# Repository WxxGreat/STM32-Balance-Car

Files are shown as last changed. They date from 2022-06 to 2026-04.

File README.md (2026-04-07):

# 0. 关于本项目

本项目使用`STM32F103C8T6`作为主控，`Keil5`开发，`Mahony`算法进行姿态解算的平衡车。项目中给出了`MPU6050`、`ICM20602`、`ICM42605`三种主流IMU的驱动。目前仅实现了直立平衡，建议当成工程模板使用。
 (＠_＠;)

# 1. 硬件

## 1.1 PCB 

目前是第一版，用到的都是插接件。后续还会更新PCB（计划换成贴片，体积会更小）

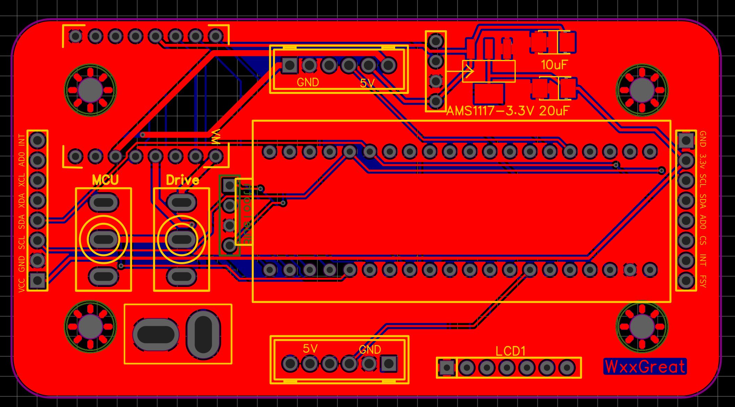
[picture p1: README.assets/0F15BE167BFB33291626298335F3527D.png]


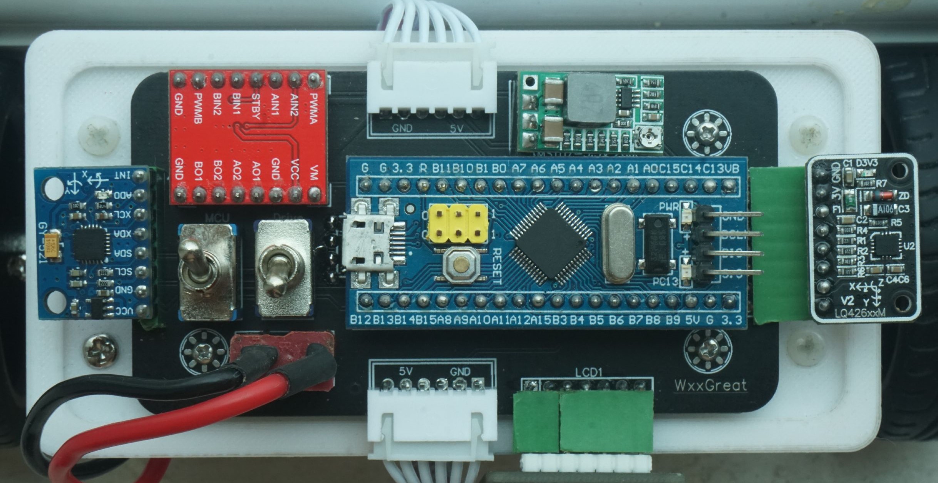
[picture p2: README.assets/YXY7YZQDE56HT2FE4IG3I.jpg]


## 1.2 车模

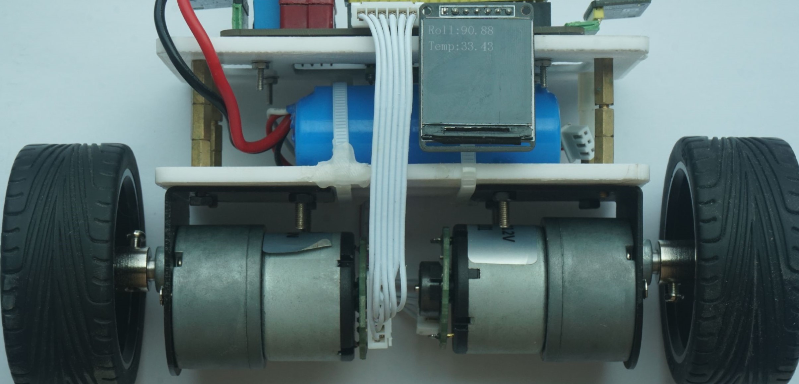
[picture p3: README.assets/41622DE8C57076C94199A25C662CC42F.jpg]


`LCD`使用1.3寸`ST7789`主控 `240×240`分辨率

电机型号`MG513P20_12V` ，我买的淘宝店：[直流减速电机带光电霍尔编码器码盘测速两轮自平衡小车 ](https://item.taobao.com/item.htm?spm=a1z10.3-c-s.w4002-15726392041.27.16a3143eqzsQfR&id=45347924687 )*

电池链接：[恩智浦智能汽车竞赛 正品BCDEFHLM车模2S锂电池及充电器](https://item.taobao.com/item.htm?spm=a1z10.3-c-s.w4002-22508770840.25.3b1949cceHXuh9&id=610152052172 )*

SolidWorks画的简单底板尺寸如图，用3D打印机制造

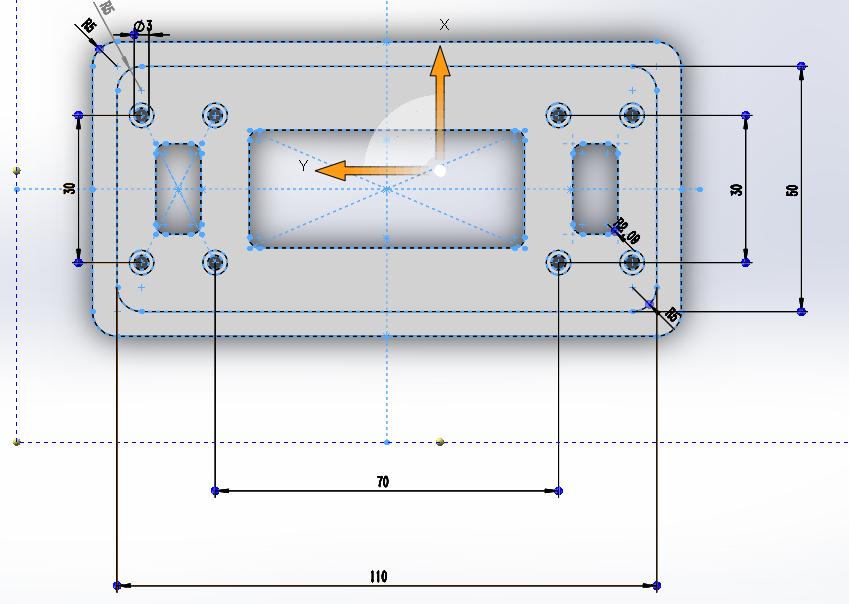
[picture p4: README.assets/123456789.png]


# 2. 算法

## 2.1 `PID`算法

####   2.1.1理论分析

该项目为使的小车平衡最主要的两个环就是直立环和速度环，通过叠加得到最终给电机的输出，这也是网上绝大多数的小车平衡控制方法。

1. 我们先使用常规的速度负反馈算法想象一下。首先我们给定一个目标速度值，由于小车在直立控制的作用下，此时小车要向前倾斜以获取加速度，车轮需要往后运动，这样小车速度就会下降。因为是负反馈,速度下降之后，速度控制的偏差增大，小车往前倾斜的角度增大，如此反复，小车便会倒下。
2. 为保证直立控制的优先级，我们把速度控制放在直立控制的前面，也就是速度控制调节的结果仅仅是改变直立控制的目标值。因为根据经验可知，小车的运行速度和小车的倾角是相关的。比如要提高小车向前行驶的速度，就需要增加小车向前倾斜的角度，倾斜角度加大之后，车轮在直立控制的作用下需要向前运动。因此直立环的`Kp`后面乘的值并不是`当前角度-机械中值`，而是一个我们速度的期望。**（这个理解了很重要！！！！）**

$$
a_1=Kp*(\theta-a_2)+Kd*\theta'  \qquad···································①直立环
$$

$$
a_2=Kp_1* Err_{speed}+Ki_1 * \sum Err_{speed}\space   \qquad····························②速度环
$$

**合并一下就可以得到：**

$$
a=Kp*(\theta)+Kd*\theta'-Kp \left [kp_1 * Err_{speed}+ki_1 * \sum Err_{speed} \right ] \qquad········③最终式
$$

因此在代码实现上我们就可以实现两个环的直接相加或相减，在`TIM3`定时器中`10ms`一个周期进行控制。

```c
      Balance_PID_Result = Position_PID_Cal(&Balance_PID, imu.Roll + 0.3f);
      if (Time_GAP_20ms) Velocity_PID_Result = Position_PID_Cal(&Velocity_PID, Velocity);

      PID_Result = Balance_PID_Result + Velocity_PID_Result;
      Set_Motor_Speed(PID_Result, PID_Result);
```

####   2.1.2调参经验

根据上边的分析我们只需要分别调整直立环的`Kp，kd`和速度环的`Kp，Ki`

1. 对于直立环的`Kp`，是调整最方便观察现象的，太小时小车没有足够的恢复力，太大时小车会在中值附近大幅震荡，调整到一个略微震荡的值即可
2. 直立环的`Kd`作用是减小低频振荡，但`Kd`太大小车又会造成高频振动，从小到大增大`Kd`，直到小车出现小幅高频振荡
3. 直立环调整结束后小车可以平衡，但受到扰动便会往一个方向疯跑，现在引入直立环
4. 网上查到的资料对于速度环`Ki = Kp/200` ，但在我的实际调整中最终确定了`Ki = Kp/100`，这个看自己小车了，可以先按照`Ki = Kp/200`去调
5. 先将直立环`Kp，Kd`同时×0.8。调整速度环`Kp`，速度环`Kp`越大，小车便越不会出现向一个方向狂奔的情况（因为速度被速度环控住了），但会减弱直立环的控制效果，因此调整到一个车受到干扰会摇摇晃晃停下的一个状态。
6. 摇摇晃晃的原因就是因为速度环`Kp`太大，回调速度环`Kp`，并且增大直立环`Kd`（想想`Kd`的作用是什么呢？）

**以上就是我调参的经验，可以参考，最好可以理解原理再去上手实践。**

## 2.2 `Mahony`算法

**参考一篇文章：[基于Manony滤波算法的姿态解算](https://blog.csdn.net/weixin_44821644/article/details/108542178)**

###   2.2.1IMU（以MPU6050举例）

`MPU6050`是一个集成了陀螺仪和加速度计的传感器，它能输出在直角坐标系下的`x，y，z`轴的角速度和加速度数据。

陀螺仪输出的格式为：绕`x`轴的旋转角速度，绕`y`轴的角速度，绕`z`轴的角速度（分别称为`roll`角速度，pitch角速度和`yaw`角速度）。

加速度计输出的格式为：`x`轴的加速度，`y`轴的加速度，`z`轴的加速度。

另外还需要关注传感器的其他参数如：

- 陀螺仪的量程：`eg.±2000dps`
- 加速度计的量程：`eg.±2g`
- `ADC`转换精度为`16bit`
- 传感器采样率`4-1000hz：eg.1000hz`

我们从IMU那就得到了陀螺仪数据`gx,gy,gz`，加速度数据`az,ay,az`

螺仪转换精度**2^16=65536   ,  65536/{2000-(-2000)}=16.4,实际1°等于ADC值16.4**

采样率就是数据的更新率，也就是我们每次读取数据的频率。

首先将陀螺仪的数据转换成角度，这里封装成一个函数

###   2.2.2算法实现

```c
static void Get_IMU_Values(float *values)
{
	int16_t gyro[3],acc[3];
	IMU_readGyro_Acc(&gyro[0],&acc[0]);
	for(int i=0;i<3;i++)
	{
        //gyro range +-2000; adc accuracy 2^16=65536; 65536/4000=16.4;
		values[i]=((float) gyro[i])/16.4f;	
		values[3+i]=(float) acc[i];
	}
}
```

**然后编写函数实现计算姿态角的功能，使用四元数计算姿态角的公式在理论分析中推导：**

**其中α为绕x轴旋转角即`roll`，β为绕y轴旋转角即`pitch`，γ为绕z轴旋转角即yaw。`a,b,c,d`即`q0,q1,q2,q3`.**

```c
void IMU_Update(void)
{
	static float q[4];
	float Values[6];	
	Get_IMU_Values(Values);	
	
	//change angle to radian,the calculate the imu with Mahony
	MahonyAHRSupdateIMU(Values[0] * PI/180, Values[1] * PI/180, Values[2] * PI/180,
 	                    Values[3], Values[4], Values[5]);		
	//save Quaternion
	q[0] = q0;
	q[1] = q1;
	q[2] = q2;
	q[3] = q3;
    
	imu.ax = Values[3];
	imu.ay = Values[4];
	imu.az = Values[5];
    
	imu.Pitch_v = Values[0];
	imu.Roll_v = Values[1];
	imu.Yaw_v = Values[2];

	//calculate the imu angle with quaternion
	imu.Roll = (atan2(2.0f*(q[0]*q[1] + q[2]*q[3]),1 - 2.0f*(q[1]*q[1] + q[2]*q[2])))* 180/PI;	
	imu.Pitch = -safe_asin(2.0f*(q[0]*q[2] - q[1]*q[3]))* 180/PI;
	imu.Yaw = -atan2(2 * q1 * q2 + 2 * q0 * q3, -2 * q2*q2 - 2 * q3 * q3 + 1)* 180/PI;
}
```

**代码中`MahonyAHRSupdateIMU()`函数实现的就是四元数的更新算法。**

*逻辑上，首先用加速度计校准陀螺仪，方式是通过计算当前四元数姿态下的重力分量，与加速度计的重力分量作叉积，得到误差。
对误差作P(比例)和I(积分)运算后加到陀螺仪角速度上。最终由角速度计算新的四元数。*

**代码中的 `sampleFreq` 即执行姿态解算的频率，这里用定时器，以500HZ的频率调用`get_angle();`**

```c
void MahonyAHRSupdateIMU(float gx, float gy, float gz, float ax, float ay, float az) {
	float recipNorm;	
	float halfvx, halfvy, halfvz;	//1/2 重力分量
	float halfex, halfey, halfez;	//1/2 重力误差
	float qa, qb, qc;
	//对加速度数据归一化
	recipNorm = invSqrt(ax * ax + ay * ay + az * az);
	ax *= recipNorm;
	ay *= recipNorm;
	az *= recipNorm;

	// 由四元数计算重力分量
	halfvx = q1 * q3 - q0 * q2;
	halfvy = q0 * q1 + q2 * q3;
	halfvz = q0 * q0 - 0.5f + q3 * q3;

	// 将四元数重力分量 与 加速度计重力分量 作叉积 得到误差
	halfex = (ay * halfvz - az * halfvy);
	halfey = (az * halfvx - ax * halfvz);
	halfez = (ax * halfvy - ay * halfvx);

	//对误差作积分
	integralFBx += twoKi * halfex * (1.0f / sampleFreq);	
	integralFBy += twoKi * halfey * (1.0f / sampleFreq);
	integralFBz += twoKi * halfez * (1.0f / sampleFreq);
	//反馈到角速度
	gx += integralFBx;	     gy += integralFBy;       gz += integralFBz;

	// 对误差作比例运算并反馈
	gx += twoKp * halfex;    gy += twoKp * halfey;    gz += twoKp * halfez;

	// 计算1/2 dt
	gx *= (0.5f * (1.0f / sampleFreq));		
	gy *= (0.5f * (1.0f / sampleFreq));
	gz *= (0.5f * (1.0f / sampleFreq));
	qa = q0;     qb = q1;      qc = q2;
	// 更新四元数
	q0 += (-qb * gx - qc * gy - q3 * gz);
	q1 += (qa * gx + qc * gz - q3 * gy);
	q2 += (qa * gy - qb * gz + q3 * gx);
	q3 += (qa * gz + qb * gy - qc * gx);

	// 四元数归一化
	recipNorm = invSqrt(q0 * q0 + q1 * q1 + q2 * q2 + q3 * q3);
	q0 *= recipNorm;     q1 *= recipNorm;     q2 *= recipNorm;     q3 *= recipNorm;
}
```

**由于加速度计对水平方向的旋转无能为力，故用此程序得到的`yaw`角数据会一直漂移，无法得到校准；通常的解决方法是增加一个磁场传感器，来获得一个准确的水平方向角来校准陀螺仪的漂移。`MPU6050`支持扩展一个`IIC`接口到磁场传感器，可通过配置`MPU6050`的`IIC MASTER` 来读取磁场传感器的数据。**

在`Mahony`中提供了包含磁场数据的融合函数：

> ```C
> void MahonyAHRSupdate(float gx, float gy, float gz, float ax, float ay, float az, 
>                          float mx, float my, float mz);
> ```

## 3. 程序逻辑

首先看main函数：

```c
int main(void)
{
	All_HardWare_init();
	while (1)
	{
		Protect_Check();
		LED_show_working();
		LCD_show_Brief_info();
	}
}
```

代码都封装在了函数里，因此主控的main函数非常简单。`All_HardWare_init();`包含了所有硬件、片内资源的初始化。**因为`Mahony`每次上电融合解算姿态时需要几秒的自我校准，因此先打开定时器。**

```c
	TIM3_Int_Init(99, 7199); // 72M ÷7200 ÷100 = 10 ms
```

几秒过后再初始化PID控制器

```c
	PID_init();              //直立环，速度环PID控制器初始化
```

**`定时器3中断服务函数`在`control.c`文件中，包含姿态解算和PID控制。**

```c
void TIM3_IRQHandler(void)
{
  if (TIM_GetITStatus(TIM3, TIM_IT_Update) == SET) 
  {   TIM_ClearITPendingBit(TIM3, TIM_IT_Update);             
     /**
      *PID控制与姿态解算部分，详情请TP至
      *....../主控程序/HARDWARE/control/control.c
      *
      */
  }
}
```

死循环中目前三个函数分别是LED、LCD状态显示和 一个简易的过倾保护。

```c
void Protect_Check(void)
{
	if (imu.Roll > 30 || imu.Roll < -30)
		Protect = 1;
	else
		Protect = 0;
}
```

## 4. 补充

> ```
> NULL
> ```

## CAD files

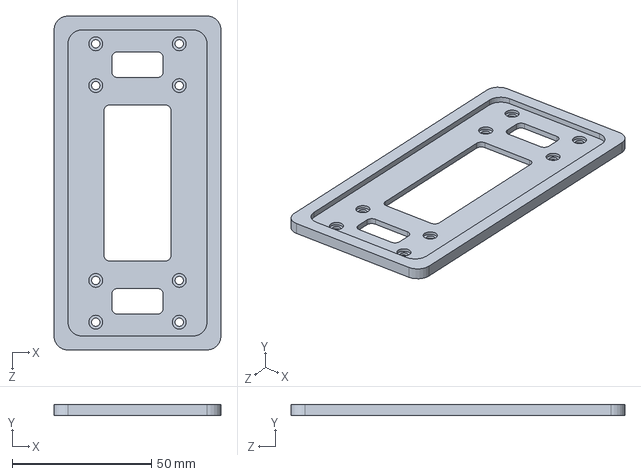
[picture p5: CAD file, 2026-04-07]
Solidworks Models/平衡车顶.SLDPRT
60.0 x 4.00 x 120.0 mm

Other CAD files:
Solidworks Models/板子.STL
Solidworks Models/平衡车.SLDPRT
Solidworks Models/平衡车.STL

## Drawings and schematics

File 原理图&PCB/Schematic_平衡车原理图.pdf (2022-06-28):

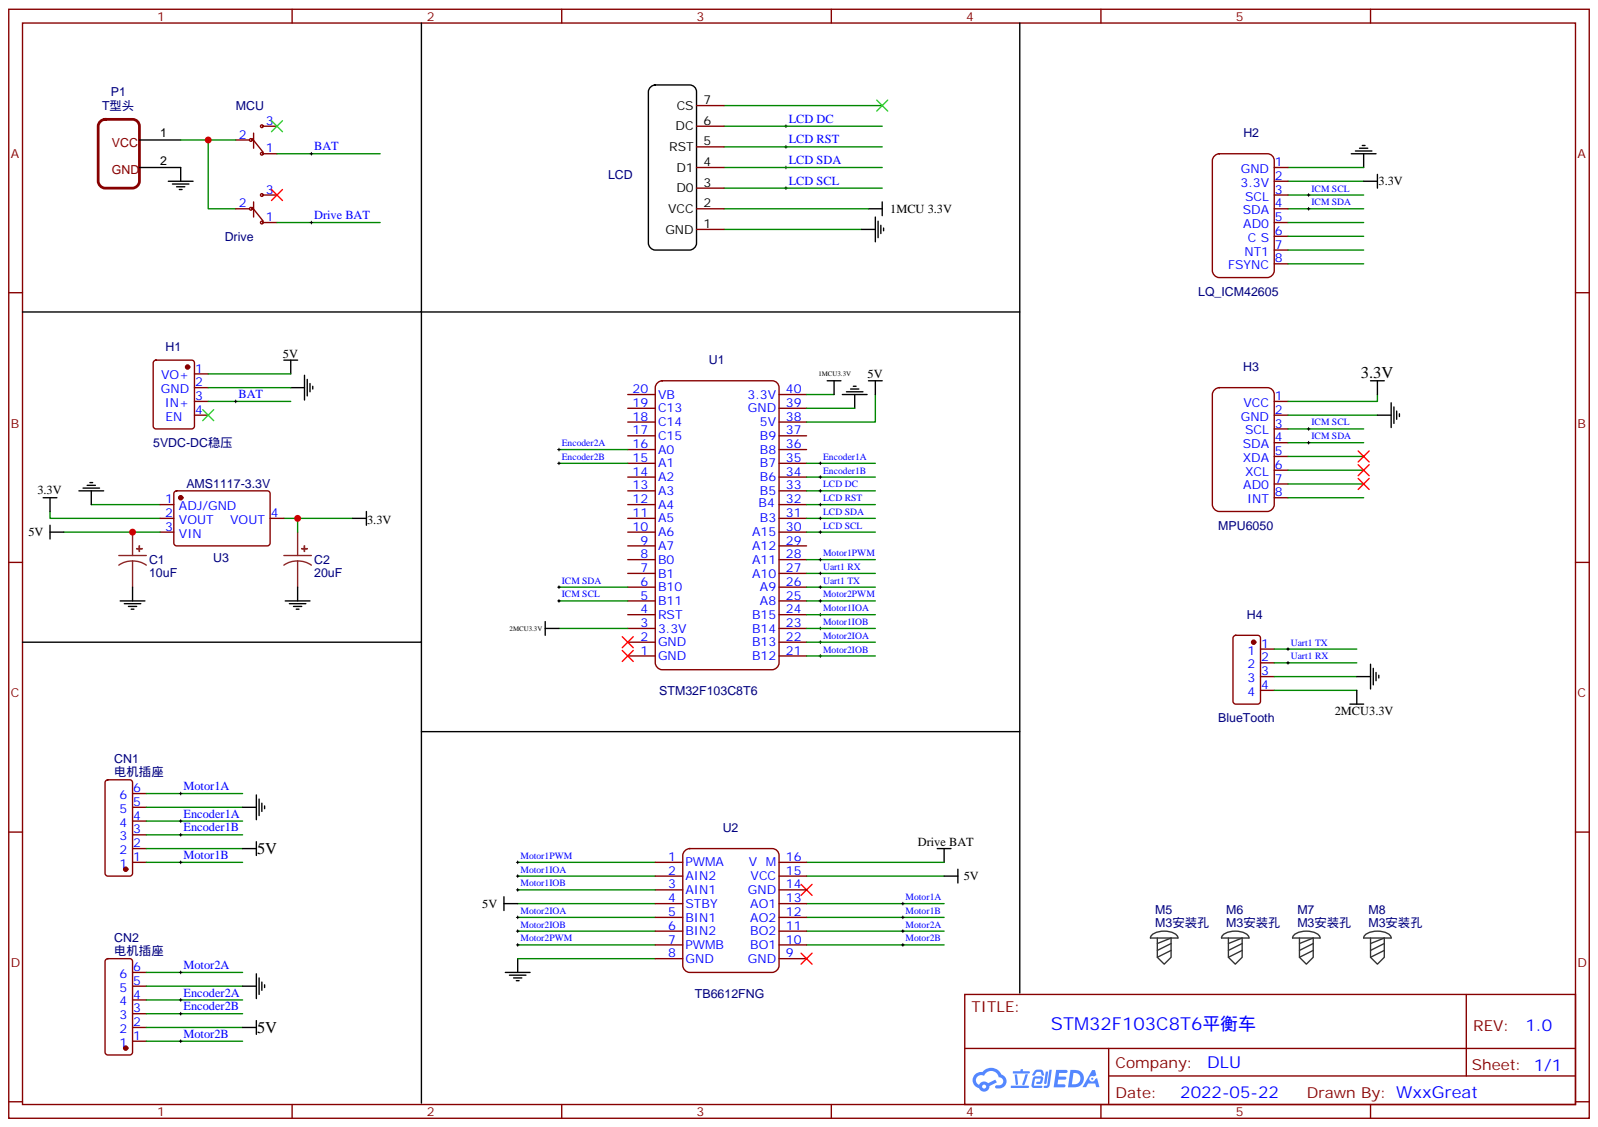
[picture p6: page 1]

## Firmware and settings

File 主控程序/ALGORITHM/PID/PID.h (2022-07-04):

#ifndef __PID_H
#define __PID_H

//PID输出范围宏定义
#define DEFAULT_PID_OUT_MAX ( 7100)
#define DEFAULT_PID_OUT_MIN (-7100)

//PID积分范围宏定义
#define DEFAULT_PID_INTEGRAL_OUT_MAX (7000)
#define DEFAULT_PID_INTEGRAL_OUT_MIN (-7000)


//定义结构体
typedef struct
{
    float SetPoint;    // 设定目标
    float Kp;          // 比例常数
    float Ki;          // 积分常数
    float Kd;          // 微分常数
    float SumError;    // 积分和
    float Error;       // 误差
    float LastError;   // 上次误差
    float PrevError;   // 前一次误差
    float LastResult;  // 上次计算结果
    float Result;      // 当前计算结果
    float OutMax;      // 输出限幅最大值
    float OutMin;      // 输出限幅最小值
    float IntegralMax; // 积分限幅最大值
    float IntegralMin; // 积分限幅最小值
} PID;


void PID_Init(PID *s_PID, float set_point, float Kp, float Ki, float Kd); //PID初始化

void PID_Set_out_Range(PID *s_PID, float outMax, float outMin);         //设置PID输出范围
void PID_Set_Integral_out_Range(PID *s_PID, float outMax, float outMin); //设置PID积分范围
void PID_SetPoint(PID *s_PID, float set_point);                              //设置目标值

float Increment_PID_Cal(PID *s_PID, float now_point); //增量式PID计算
float Position_PID_Cal(PID *s_PID, float now_point);  //位置式PID计算
float PID_Cal(PID *s_PID, float now_point);           //比例外置式PID

float Balance_Car_Velocity_ONLY_Position_PID_Cal(PID *s_PID, float now_point , unsigned char State_Flag);

void PID_Integral_limit(PID *s_PID, float *IOutValue);
void PID_Output_limit(PID *s_PID, float *Result);
float Yaw_PID(PID *s_PID, float now_point); //


#endif

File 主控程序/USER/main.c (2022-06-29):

#include "sys.h"

/**
 * @brief          使用Mahony进行姿态解算的平衡车
 *
 * @note           Forkde from my former project "MPU6050 DMP Demo For STM32F10x" 
 *
 * @date           2021-8-20 16:32
 *
 * @LastEditTime   2022-6-28 16:05
 *
 * @author         WxxGreat
 *
 * @version        1.0 仅可以平衡  
 */

int main(void)
{
	All_HardWare_init();
	while (1)
	{
		Protect_Check();
		LED_show_working();
		LCD_show_Brief_info();
	}
}

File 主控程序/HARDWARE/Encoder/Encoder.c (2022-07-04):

#include "encoder.h"

void Encoder_Init_TIM2(void)
{
	TIM_TimeBaseInitTypeDef TIM_TimeBaseStructure;  
  TIM_ICInitTypeDef TIM_ICInitStructure;  
  GPIO_InitTypeDef GPIO_InitStructure;

	
  GPIO_InitStructure.GPIO_Pin = GPIO_Pin_0|GPIO_Pin_1;	//端口配置
  GPIO_InitStructure.GPIO_Mode = GPIO_Mode_IN_FLOATING; //浮空输入
  GPIO_Init(GPIOA, &GPIO_InitStructure);					      //根据设定参数初始化GPIOB
  
  TIM_TimeBaseStructInit(&TIM_TimeBaseStructure);
  TIM_TimeBaseStructure.TIM_Prescaler = 0x0; // 预分频器 
  TIM_TimeBaseStructure.TIM_Period = 65535; //设定计数器自动重装值
  TIM_TimeBaseStructure.TIM_ClockDivision = TIM_CKD_DIV1;//选择时钟分频：不分频
  TIM_TimeBaseStructure.TIM_CounterMode = TIM_CounterMode_Up;////TIM向上计数  
  TIM_TimeBaseInit(TIM2, &TIM_TimeBaseStructure);
	
  TIM_EncoderInterfaceConfig(TIM2, TIM_EncoderMode_TI12, TIM_ICPolarity_Rising, TIM_ICPolarity_Rising);//使用编码器模式3
  TIM_ICStructInit(&TIM_ICInitStructure);
  TIM_ICInitStructure.TIM_ICFilter = 10;
  TIM_ICInit(TIM2, &TIM_ICInitStructure);
  TIM_ClearFlag(TIM2, TIM_FLAG_Update);//清除TIM的更新标志位
  TIM_ITConfig(TIM2, TIM_IT_Update, ENABLE);
  //Reset counter
  //TIM_SetCounter(TIM2,0);
  TIM_Cmd(TIM2, ENABLE); 
	TIM_SetCounter(TIM2,0);
}
/**************************************************************************
q**************************************************************************/
void Encoder_Init_TIM4(void)
{
	TIM_TimeBaseInitTypeDef TIM_TimeBaseStructure;  
  TIM_ICInitTypeDef TIM_ICInitStructure;  
  GPIO_InitTypeDef GPIO_InitStructure;

  GPIO_InitStructure.GPIO_Pin = GPIO_Pin_6|GPIO_Pin_7;	//端口配置
  GPIO_InitStructure.GPIO_Mode = GPIO_Mode_IN_FLOATING; //浮空输入
  GPIO_Init(GPIOB, &GPIO_InitStructure);					      //根据设定参数初始化GPIOB
  
  TIM_TimeBaseStructInit(&TIM_TimeBaseStructure);
  TIM_TimeBaseStructure.TIM_Prescaler = 0x0; // 预分频器 
  TIM_TimeBaseStructure.TIM_Period = 65535; //设定计数器自动重装值
  TIM_TimeBaseStructure.TIM_ClockDivision = TIM_CKD_DIV1;//选择时钟分频：不分频
  TIM_TimeBaseStructure.TIM_CounterMode = TIM_CounterMode_Up;////TIM向上计数  
  TIM_TimeBaseInit(TIM4, &TIM_TimeBaseStructure);
	
  TIM_EncoderInterfaceConfig(TIM4, TIM_EncoderMode_TI12, TIM_ICPolarity_Rising, TIM_ICPolarity_Rising);//使用编码器模式3
  TIM_ICStructInit(&TIM_ICInitStructure);
  TIM_ICInitStructure.TIM_ICFilter = 10;
  TIM_ICInit(TIM4, &TIM_ICInitStructure);
  TIM_ClearFlag(TIM4, TIM_FLAG_Update);//清除TIM的更新标志位
  TIM_ITConfig(TIM4, TIM_IT_Update, ENABLE);
  //Reset counter
  //TIM_SetCounter(TIM4,0);
  TIM_Cmd(TIM4, ENABLE); 
	TIM_SetCounter(TIM4,0);
}

/**************************************************************************
函数功能：单位时间读取编码器计数
入口参数：定时器
返回  值：速度值
**************************************************************************/
int16_t Read_Encoder(u8 TIMX)
{
   int16_t Encoder_TIM;    
   switch(TIMX)
	 {
	   case 2:  Encoder_TIM= -(short)TIM2 -> CNT;  TIM2 -> CNT=0;break;
		 case 3:  Encoder_TIM=  (short)TIM3 -> CNT;  TIM3 -> CNT=0;break;	
		 case 4:  Encoder_TIM= -(short)TIM4 -> CNT;  TIM4 -> CNT=0;break;	
		 default: Encoder_TIM=0;
	 }
		return Encoder_TIM;
}

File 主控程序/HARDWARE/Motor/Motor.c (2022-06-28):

#include "Motor.h"


void Set_Motor_Speed(int16_t Left,int16_t Right)
{
	if(Left >= 0)
	{
	 TIM1->CCR4 = Left;
	 AIN1 = 0;
	 AIN2 = 1;
	}
	else	
	{
	 TIM1->CCR4 = -Left;
	 AIN1 = 1;
	 AIN2 = 0;
	}

	if(Right >= 0)
	{
	 TIM1->CCR1 = Right;
	 BIN1 = 0;
	 BIN2 = 1;
	}
	else	
	{
	 TIM1->CCR1 = -Right;
	 BIN1 = 1;
	 BIN2 = 0;
	}

}


void TIM1_Motor_PWM_Init(u16 arr,u16 psc)
{		 		
	GPIO_InitTypeDef GPIO_InitStructure;
	TIM_TimeBaseInitTypeDef  TIM_TimeBaseStructure;
	TIM_OCInitTypeDef  TIM_OCInitStructure;


   //设置该引脚为复用输出功能,输出TIM1 CH1 CH4的PWM脉冲波形
	GPIO_InitStructure.GPIO_Pin = GPIO_Pin_8|GPIO_Pin_11; //TIM1_CH1 、CH4
	GPIO_InitStructure.GPIO_Mode = GPIO_Mode_AF_PP;  //复用推挽输出
	GPIO_InitStructure.GPIO_Speed = GPIO_Speed_50MHz;
	GPIO_Init(GPIOA, &GPIO_InitStructure);
	
	TIM_TimeBaseStructure.TIM_Period = arr; //设置在下一个更新事件装入活动的自动重装载寄存器周期的值	 
	TIM_TimeBaseStructure.TIM_Prescaler =psc; //设置用来作为TIMx时钟频率除数的预分频值  不分频
	TIM_TimeBaseStructure.TIM_ClockDivision = 0; //设置时钟分割:TDTS = Tck_tim
	TIM_TimeBaseStructure.TIM_CounterMode = TIM_CounterMode_Up;  //TIM向上计数模式
	TIM_TimeBaseInit(TIM1, &TIM_TimeBaseStructure); //根据TIM_TimeBaseInitStruct中指定的参数初始化TIMx的时间基数单位

 
	TIM_OCInitStructure.TIM_OCMode = TIM_OCMode_PWM1;             //选择定时器模式:TIM脉冲宽度调制模式1
	TIM_OCInitStructure.TIM_OutputState = TIM_OutputState_Enable; //比较输出使能
	TIM_OCInitStructure.TIM_Pulse = 0;                            //设置待装入捕获比较寄存器的脉冲值
	TIM_OCInitStructure.TIM_OCPolarity = TIM_OCPolarity_High;     //输出极性:TIM输出比较极性高
	
	TIM_OC1Init(TIM1, &TIM_OCInitStructure);  //根据TIM_OCInitStruct中指定的参数初始化外设TIMx
	TIM_OC4Init(TIM1, &TIM_OCInitStructure);  //根据TIM_OCInitStruct中指定的参数初始化外设TIMx

  TIM_CtrlPWMOutputs(TIM1,ENABLE);	//MOE 主输出使能	

	TIM_OC1PreloadConfig(TIM1, TIM_OCPreload_Enable);  //CH1预装载使能	 
	TIM_OC4PreloadConfig(TIM1, TIM_OCPreload_Enable);  //CH4预装载使能		
	
	TIM_ARRPreloadConfig(TIM1, ENABLE); //使能TIMx在ARR上的预装载寄存器
	
	TIM_Cmd(TIM1, ENABLE);  //使能TIM1
} 



void Motor_Dir_Init(void)
{
	RCC->APB2ENR |= 1 << 3;	  //PORTB时钟使能
	GPIOB->CRH &= 0X0000FFFF; //PORTB12 13 14 15推挽输出
	GPIOB->CRH |= 0X22220000; //PORTB12 13 14 15推挽输出
}

void MotorDriver_Init(void)
{
  TIM1_Motor_PWM_Init(7199,0);
	Motor_Dir_Init();
}

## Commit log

2022-06-28 Version1.0 仅可平衡，未加其他功能
2022-06-29 Version 1.0 修改了Readme
2022-07-04 更新PCB
2022-07-04 更新了PCB
2026-04-07 Add SW Model Files
    [平衡车.SLDPRT, 平衡车.STL, 平衡车顶.SLDPRT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]
